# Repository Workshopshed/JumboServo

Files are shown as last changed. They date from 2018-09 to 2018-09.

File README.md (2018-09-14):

# JumboServo
## A jumbo sized servo controlled with I2C

This project was created provide the motion for the Robotic Water Sentry (aka Triffid) and control the motion of the nozzle. 

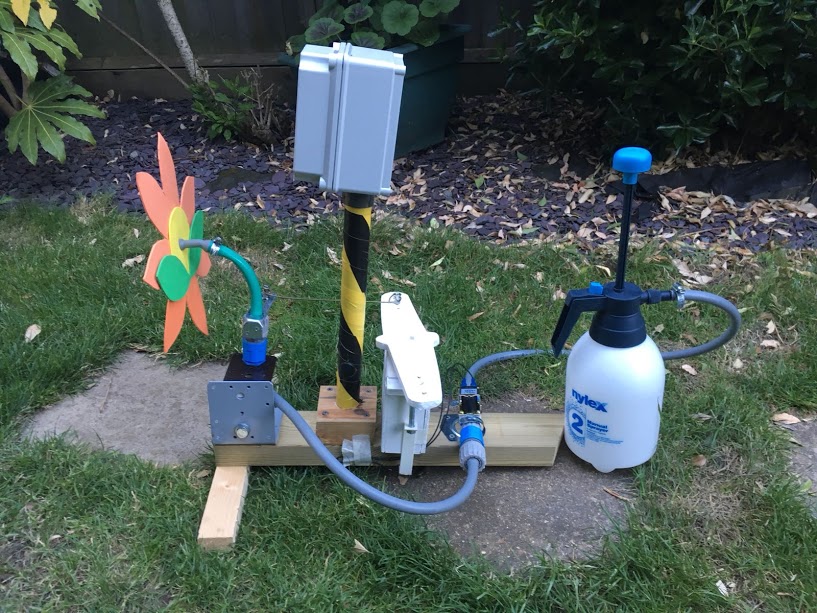
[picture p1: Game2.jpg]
Squirting water game


As big servos were expensive I thought I could build one from an Arduino, Potentiometer and and small Motor with Gearbox.

## Parts

* Adafruit 5v Itsybitsy
* L298 H-Bridge module
* 10K Linear Potentiometer
* 2x 220R resistor
* 0.1uF Capacitor
* Wire
* Connectors
* Motor with gearbox

Along with the electronics is a metal plate to hold the motor and potentiometer and a wooden case styled in the design of a servo. I used a [MFA/COMODRILLS 919D motor gearbox](https://www.mfacomodrills.com/gearboxes/919d_series.html).

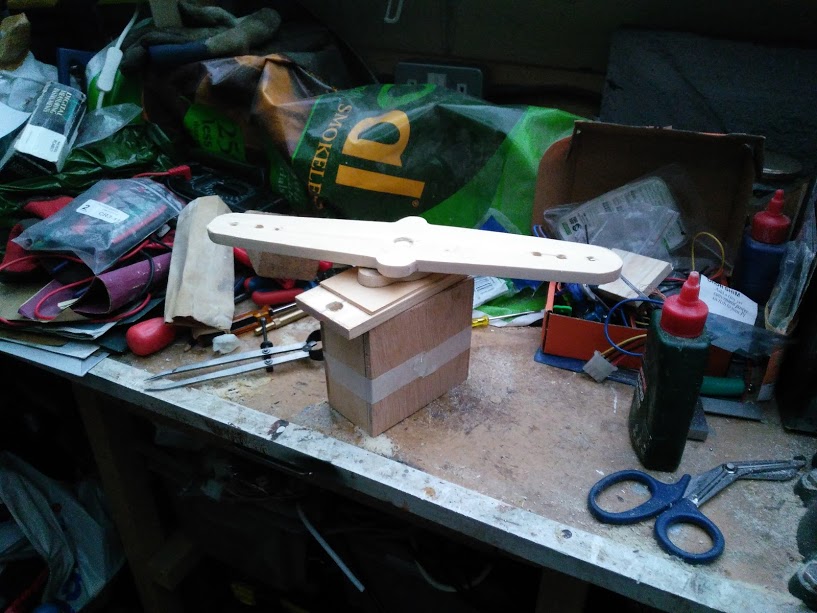
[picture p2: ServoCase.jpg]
Servo Case


## Electronics

The schematic for the project is provided in KiCad format.

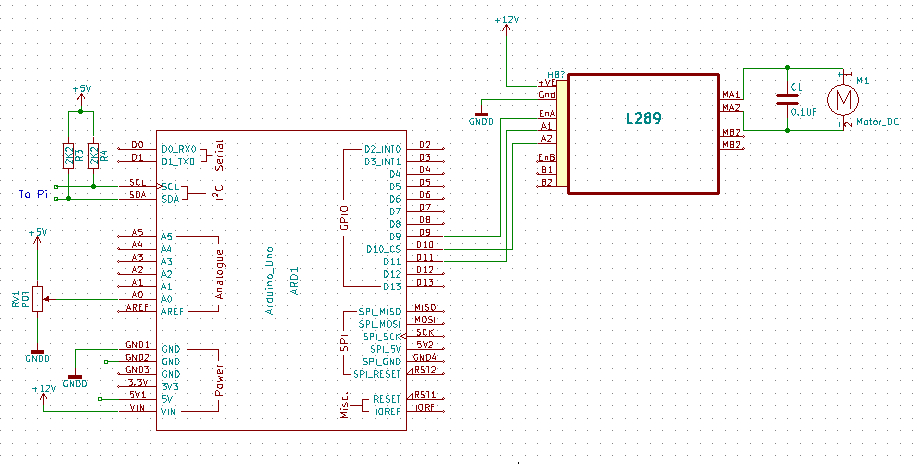
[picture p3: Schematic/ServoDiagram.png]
Schematic Servo Diagram


The key points are that the enable wire for the H-Bridge module should be one of the PWM enabled pins on your Arduino. The two control pins should be determined so that when the motor is running forward the values from the analogue input increments and vice-versa. It's recommended that you test this with the gear for the potentiometer disconnected.

A 0.1uF capacitor is wired across the contacts of the motor to help surpress noise from the motor.

The i2C cable will need some pullup resistors. The value of these will depend on the length of the cable. The longer the cable the lower values are recommended. At 0.5 I used a 220R resistor. Cables over 1m may not work at all.

## Code

There's two lots of code here. The "Servo" folder is the code that runs on the servo and the "Controller" folder is demo project for a test rig with uses an LCD and some buttons to control the servo.

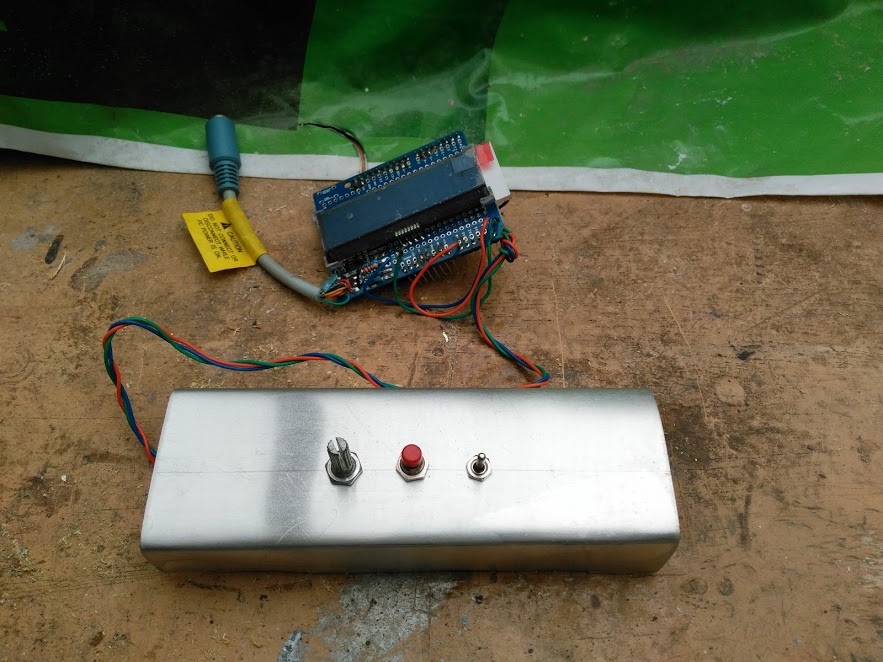
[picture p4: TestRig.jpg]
Test Rig


## Protocol

The servo takes 3 commands from the controller.

|Command|Value|Data Bytes|
|---|---|---|
|Stop |1|0|
|Angle|2|2|
|Speed|3|2|

For the angle and speed commands the command value is followed by the value as an integer with the low byte first. Angle is a value from 0-1023, the controller needs to compensate for this and turn the value into degrees. Note that for the current version speed is just from 0-255 so a 0 should be sent as the high byte. Low values of speed should be avoided typically the motor won't turn.

One of the reasons for having a digital protocol is to be able to read the status back from the servo. This is done by requesting a read from the registers.

|Register|Value|Description|
|---|---|---|
|Target|0|Where the motor is aiming to get to?|
|Running|1|Is the motor currently running?|
|Position|2|Current output shaft position|
|Speed|3|Speed|
|Direction|4|Current direction of movement|

## 3D Models

There are two models provide the gear to fit the potentiometer and the spindle for the output shaft. These were built using OpenSCAD. Note that you may need to adjust the internal size of the gear and spindle to get a good fit on your pot/motor output shaft.

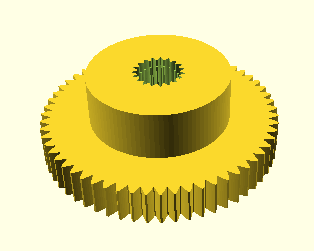
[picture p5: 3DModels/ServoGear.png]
Servo Gear
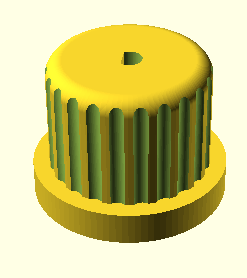
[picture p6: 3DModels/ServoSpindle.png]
Servo Spindle


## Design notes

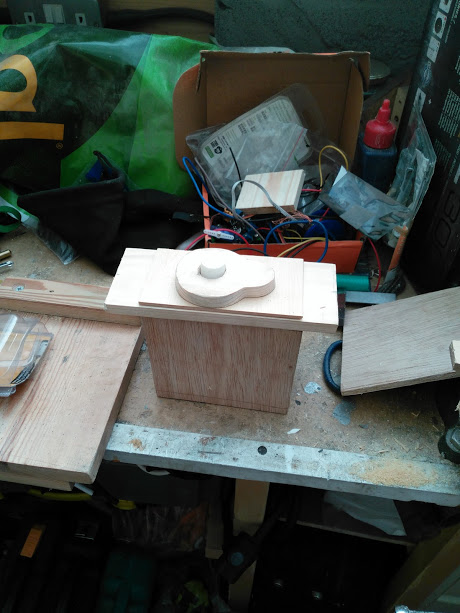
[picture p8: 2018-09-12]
ServoCase2.jpg

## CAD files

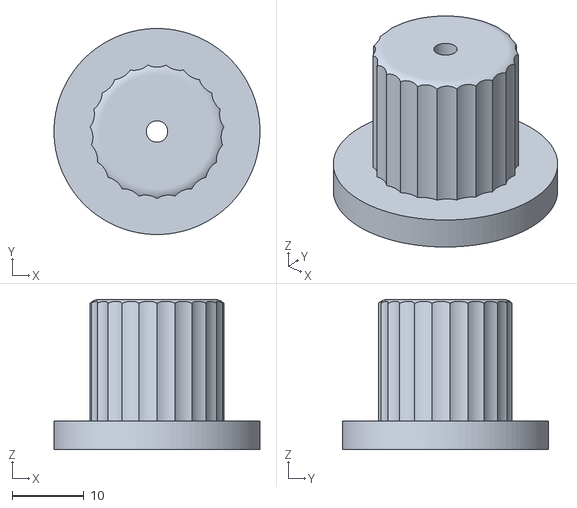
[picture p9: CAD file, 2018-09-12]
3DModels/ServoSpindle.stl
28.8 x 28.8 x 21.0

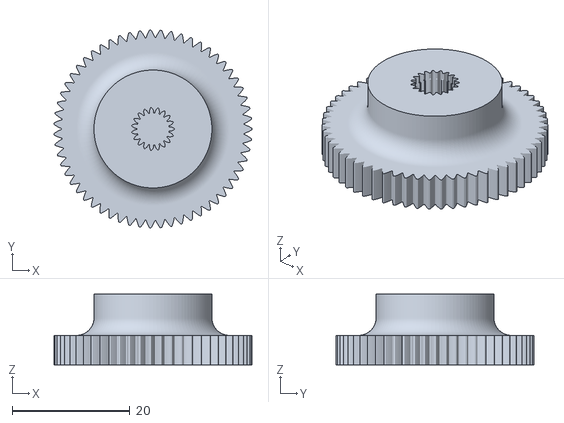
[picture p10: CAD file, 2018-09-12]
3DModels/ServoGear.stl
33.6 x 33.6 x 12.0

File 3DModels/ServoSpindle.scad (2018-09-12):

//Servo Spindle

module ForCircle(offset,num) {
    angle = 360 / num;
    for (i = [1:num] )
        {
            rotate([0,0,angle*i])
                translate([0,offset,0])
                    children();
        }
}

module Torus(r1,r2) {
    rotate_extrude(angle = 360, convexity = 2)
        translate([r2,0,0])
            circle(r=r1);
}

module DrillWithFlat(rdrill,height) {
    flat = rdrill*2;
    difference(){
        cylinder(h=height,r=rdrill);
        translate([rdrill*0.8,-flat/2,-1])
            cube([flat,flat,height+2]);
    }
}

module Spindle()
{
rmajor = 12;
hknurlled = 15;
rtorus = 2;
rindent = 3;
rdrill = 3.15;
hflange =4;
difference() {
    union() {
        difference() {
            union() {
                translate([0,0,hknurlled])
                    Torus(rtorus,rmajor-(2*rtorus));
                cylinder(h=hknurlled,r=rmajor);
                cylinder(h=hknurlled+rtorus,r=rmajor-(2*rtorus));
            }
            ForCircle(hknurlled-rindent,23) {
                translate([0,0,-1])
                    cylinder(h=hknurlled + rtorus + 2,r=rindent);
                }
            }
        translate([0,0,-hflange])
            cylinder(h=hflange,r=rmajor*1.2);
        }
    translate([0,0,-hflange-7]) {
        DrillWithFlat(rdrill,hknurlled + rtorus+1 );
    }
    translate([0,0,hknurlled-hflange-9]) {
        cylinder(h=40,r=1.5);
        } 
    }  
            
}

module drillTest() {
    difference() {
        cylinder(h=3,r=8);
        translate([0,0,-15])
            #DrillWithFlat(3.2, 20);
    }
}

$fn = 100;
Spindle();

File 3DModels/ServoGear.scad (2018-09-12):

// Copyright 2011 Cliff L. Biffle.
// This file is licensed Creative Commons Attribution-ShareAlike 3.0.
// http://creativecommons.org/licenses/by-sa/3.0/

// You can get this file from http://www.thingiverse.com/thing:3575
use <parametric_involute_gear_v5.0.scad>

// Couple handy arithmetic shortcuts
function sqr(n) = pow(n, 2);
function cube(n) = pow(n, 3);

// This was derived as follows:
// In Greg Frost's original script, the outer radius of a spur
// gear can be computed as...
function gear_outer_radius(number_of_teeth, circular_pitch) =
	(sqr(number_of_teeth) * sqr(circular_pitch) + 64800)
		/ (360 * number_of_teeth * circular_pitch);

// We can fit gears to the spacing by working it backwards.
//  spacing = gear_outer_radius(teeth1, cp)
//          + gear_outer_radius(teeth2, cp);
//
// I plugged this into an algebra system, assuming that spacing,
// teeth1, and teeth2 are given.  By solving for circular pitch,
// we get this terrifying equation:
function fit_spur_gears(n1, n2, spacing) =
	(180 * spacing * n1 * n2  +  180
		* sqrt(-(2*n1*cube(n2)-(sqr(spacing)-4)*sqr(n1)*sqr(n2)+2*cube(n1)*n2)))
	/ (n1*sqr(n2) + sqr(n1)*n2);


module servo_gear() {
    $fn = 100;
	n1 = 38; n2 = 59;
	p = fit_spur_gears(n1, n2, 26.8);
    //p=129.3875;
	// Simple Test:
	/* gear (circular_pitch=p,
		gear_thickness = 3,
		rim_thickness = 3,
		hub_thickness = 3,
	    number_of_teeth = n1,
		circles=8);
	
	translate([gear_outer_radius(n1, p) +   gear_outer_radius(n2, p),0,0])
    */
    
    difference() {
        
    union() {
    //fillet
    difference() {
        cylinder(d=26,h=8);
        translate([0,0,8])
            torus(3,13);
    }    
	gear (circular_pitch=p,
		gear_thickness = 5,
		rim_thickness = 5,
		hub_thickness = 12,
    	hub_diameter=20,
        bore_diameter=0,
		circles=0,
		number_of_teeth = n2,
		rim_width = 1);
    }
        
        
    translate([0,0,4])
        splinegear();
    translate([0,0,11])
        cylinder(d=6,h=10);
        
    }
}

module testgear()
{
        n1 = 38; n2 = 59;
        p = fit_spur_gears(n1, n2, 26.8);
        //  96.4527;
        //p=96.4527;
        //14.7358
        $fn = 100;
        
        echo ("Module:",p);
    difference() {
    	gear (circular_pitch=p,
		gear_thickness = 2,
		rim_thickness = 2,
		hub_thickness = 2,
    	hub_diameter=20,
        bore_diameter=0,
		circles=0,
		number_of_teeth = n2,
		rim_width = 1);
        translate([-7,-5,1.5]) linear_extrude(height=3,convexity = 10, twist = 0) text(text=str(n2));
    }
}

module splinegear() {
    n1 = 38; n2 = 59;
	p = fit_spur_gears(n1, n2, 27);
    gear (circular_pitch=p/1.6,
            gear_thickness = 10,
            rim_thickness = 10,
            hub_thickness = 5,
            bore_diameter=0,
            circles=0,
            number_of_teeth = 19,
            rim_width = 10);
}

module splinetest() {
    $fn = 100;
	n1 = 38; n2 = 59;
	p = fit_spur_gears(n1, n2, 27);
    difference() {
        cylinder(d=10,h=6);
        translate([0,0,2])
            splinegear();
    }
}

module torus(r1,r2) {
    rotate_extrude(angle = 360, convexity = 2)
        translate([r2,0,0])
            circle(r=r1);
}

//splinetest();
servo_gear();
//projection(cut = true)
//    translate([0,0,-2])
//testgear();

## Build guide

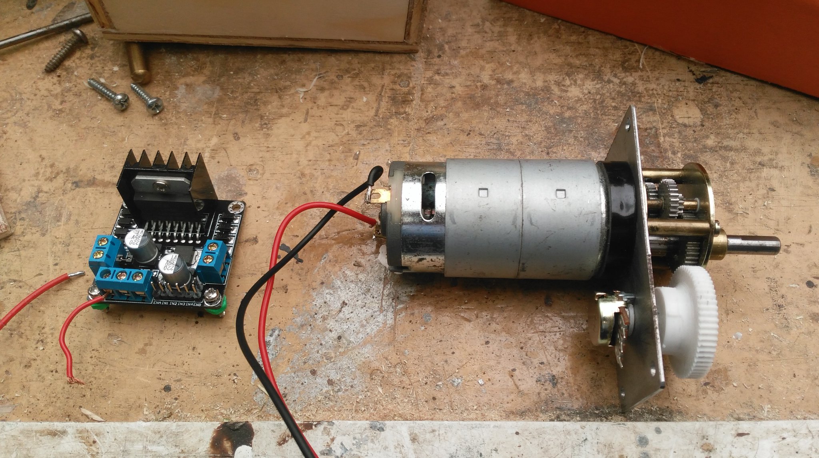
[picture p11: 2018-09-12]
WiringTheMotor.jpg

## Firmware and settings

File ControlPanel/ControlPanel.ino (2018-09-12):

#include <Wire.h>
#include "ST7036.h"
#include "bin.h"
#include "PinChangeInt.h"

//Hardware required:
//1: I2C LCD connected on standard pins
//2: Linear Pot connected on analog pin 1
//3: Jumbo Servo on I2C
//4: Push button connected to GND and pin 9

long sensorValue = 0;  // variable to store the value coming from the sensor
long angle = 0;
ST7036 lcd = ST7036 ( 2, 16, 0x7C );                               //Gotcha with the address, needed to be shifted one to the left

const int slaveAddress = 8;
const int triggerPin = 9;
const int switchPin = 11;
const int potPin = A0;
const int speedValue = 130; // 0 to 255

volatile byte triggered = 0;

enum registers {ReadReg = 0,
                Status = 0,
                Position = 1,
                Angle = 2,
                Speed = 3}; 

const int numReadings = 10;

int readings[numReadings];      // the readings from the analog input
int readIndex = 0;              // the index of the current reading
int total = 0;                  // the running total
int average = 0;                // the average

//Large chars
char bn1[]={6,1,6, 1,6,32, 1,3,4, 3,3,4, 6,2,2,   6,3,1, 5,3,1, 1,1,4,   5,3,4, 5,3,4};
char bn2[]={6,2,6, 2,6,2,  5,2,2, 2,2,4, 32,6,32, 2,2,4, 5,2,4, 32,6,32, 5,3,4, 32,32,6};

void setup()
{
    pinMode(triggerPin, INPUT_PULLUP);  // Configure the pin as an input, and turn on the pullup resistor.
                                      // See http://arduino.cc/en/Tutorial/DigitalPins
    attachPinChangeInterrupt(triggerPin, interruptFunction, FALLING);

    lcd.init();
    lcd.on();
    lcd.setCursor(0, 0);
   
    lcd.print("Hello BCS!");
    
    loadlargechars();
    
    delay(2000);
    lcd.clear();
}

// Do not use any Serial.print() in interrupt subroutines. Serial.print() uses interrupts,
// and by default interrupts are off in interrupt subroutines. Interrupt routines should also
// be as fast as possible. Here we just increment a counter.
void interruptFunction() {
  triggered = 1;
}

void loadlargechars()
{
  uint8_t cc1[8] = { // Custom Character 1
     B8(11111),
     B8(11111),
     B8(11111),
     B8(00000),
     B8(00000),
     B8(00000),
     B8(00000),
     B8(00000)
     };

  uint8_t cc2[8] = { // Custom Character 2
     B8(00000),
     B8(00000),
     B8(00000),
     B8(00000),
     B8(00000),
     B8(11111),
     B8(11111),
     B8(11111)
     };

  uint8_t cc3[8] = { // Custom Character 3
     B8(11111),
     B8(11111),
     B8(11111),
     B8(00000),
     B8(00000),
     B8(00000),
     B8(11111),
     B8(11111)
     };

  uint8_t cc4[8] = { // Custom Character 4
     B8(11100),
     B8(11110),
     B8(11111),
     B8(11111),
     B8(11111),
     B8(11111),
     B8(11110),
     B8(11100)
     };
     
  uint8_t cc5[8] = { // Custom Character 5
     B8(00111),
     B8(01111),
     B8(11111),
     B8(11111),
     B8(11111),
     B8(11111),
     B8(01111),
     B8(00111)
     };     

  uint8_t cc6[8] = { // Custom Character 6
     B8(11111),
     B8(11111),
     B8(11111),
     B8(11111),
     B8(11111),
     B8(11111),
     B8(11111),
     B8(11111)
     };   

  uint8_t cc7[8] = { // Custom Character 7 Degree
     B8(01110),
     B8(10001),
     B8(10001),
     B8(10001),
     B8(01110),
     B8(00000),
     B8(00000),
     B8(00000)
     };  
    
    lcd.load_custom_character(1, cc1);
    lcd.load_custom_character(2, cc2);
    lcd.load_custom_character(3, cc3);
    lcd.load_custom_character(4, cc4);
    lcd.load_custom_character(5, cc5);
    lcd.load_custom_character(6, cc6);
    lcd.load_custom_character(7, cc7);
}

int getReading()
{
  total = total - readings[readIndex];
  // read from the sensor:
  readings[readIndex] = analogRead(potPin);
  // add the reading to the total:
  total = total + readings[readIndex];
  // advance to the next position in the array:
  readIndex = readIndex + 1;

  // if we're at the end of the array...
  if (readIndex >= numReadings) {
    // ...wrap around to the beginning:
    readIndex = 0;
  }

  // calculate the average:
  average = total / numReadings;
  return average;
}

void loop()
{
  if (triggered == 1) {
    lcd.clear();
    lcd.print("Sending");
    writeRegister(Speed,speedValue);
    writeRegister(Angle,sensorValue); //Values 0-1023
    delay(700);
    lcd.clear();
    lcd.print("Sent");
    delay(500);
    lcd.clear();
    display(angle);
    triggered = 0;    
  }

  
  // read the value from the sensor:
  long newValue = getReading();
  if (sensorValue != newValue) {
    // Makes the assumption that the pot turns 360 degrees, adjust the value below to compensate e.g. a 300 degree pot would be 3000
    angle = (sensorValue * 3600 / 1024); 
    display(angle);
  }
  sensorValue = newValue;

  delay(10);
}

void display(int i) //Display the value in large characters
{
  lcd.clear();  
  //lcd.print(angle);
  PrintBigDeg(15);
  if (i == 0)
  {
    PrintBigDigit(0,8);
    PrintBigDot(11);
    PrintBigDigit(0,12);
  }
  int pos = 15;
  while(i>0)
  {
    pos -= 3;
    PrintBigDigit(i % 10,pos);
    i /= 10;
    if (pos==12){
     PrintBigDot(--pos);
    }
  }
  

}

void PrintBigDigit(uint8_t digit, uint8_t offset)
{

 // Line 1 of the one digit number
 lcd.setCursor(0,offset);
 lcd.write(bn1[digit*3]);
 lcd.write(bn1[digit*3+1]);
 lcd.write(bn1[digit*3+2]);

 // Line 2 of the one-digit number
 lcd.setCursor(1,offset);
 lcd.write(bn2[digit*3]);
 lcd.write(bn2[digit*3+1]);
 lcd.write(bn2[digit*3+2]);
}

void PrintBigDot(uint8_t offset)
{
  lcd.setCursor(1,offset);
  lcd.print('.');
}
void PrintBigDeg(int8_t offset)
{
  lcd.setCursor(0,offset);
  lcd.write(7);
}

void readRegister(byte reg) {
  Serial.print("Reading register:");
  Serial.print(reg);
  
  Wire.beginTransmission(slaveAddress);
  Wire.write((uint8_t *)&reg, sizeof(reg));
  Wire.endTransmission();
  delay(100);
  Wire.requestFrom(slaveAddress, 2);    // request 2 bytes from slave device #8

  int value;
  if (Wire.available()) { // slave may send less than requested
    value = Wire.read(); // receive a byte as character
  }
  if (Wire.available()) {
    int high = Wire.read();
    value = value + (high << 8);
  }

  Serial.print("=");    
  Serial.println(value);    

  while (Wire.available()) { // clear buffer incase anything else sent
    char c = Wire.read(); // receive a byte as character
  }
  
  delay(500);
}

void writeRegister(byte command,int value) {
  Serial.print("Writing register:");
  Serial.print(command);
  Serial.print("=");    
  Serial.println(value);    
  char message[3];
  message[0] = command;
  message[1] = value;       //low Byte, high
  message[2] = value >> 8;
  Wire.beginTransmission(slaveAddress);
  Wire.write(message,3);
  Wire.endTransmission();
}

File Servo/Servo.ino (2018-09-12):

#include <Wire.h>

const int slaveAddress = 8;

const int sensePin = A0;
const int drivePin1 = 11;
const int drivePin2 = 10;
const int speedPin = 9; //Needs to support PWM

int blink = 0;

short registers[5];
int readCmd;

enum readRegisters { Target = 0,
                     Running = 1,
                     Position = 2,
                     Speed = 3,
                     Direction = 4
                   };

enum commands { CmdStop = 1,
                CmdAngle = 2,
                CmdSpeed = 3,
              };

void setup() {
  Serial.println("Initialising");
 
  stop();

  pinMode(drivePin1, OUTPUT);
  pinMode(drivePin2, OUTPUT);
  pinMode(speedPin, OUTPUT);
  pinMode(sensePin, INPUT);

  Wire.begin(slaveAddress);                // join i2c bus with address #8
  Wire.onReceive(receiveEvent); // write data
  Wire.onRequest(requestEvent); // requests to read data

}

void clearAndHome() 
{ 
  Serial.write(27); 
  Serial.print("[2J"); // clear screen 
  Serial.write(27); // ESC 
  Serial.print("[H"); // cursor to home 
} 

void loop() {
  digitalWrite(13, blink);
  blink = !blink;
  
  registers[Position] = analogRead(sensePin);

  if (registers[Running]) {
    clearAndHome();
    Serial.println(registers[Target]);
    Serial.println(registers[Position]);
    Serial.println(registers[Speed]);
    
    if (registers[Direction] == 1) {
      Serial.println("Forward");
      if (registers[Position] >= registers[Target]) {
        stop();
      }
    }
    if (registers[Direction] == -1) {
      Serial.println("Backwards");
      if (registers[Position] <= registers[Target]) {
        stop();
      }
    }
  }
}

void stop() {
  digitalWrite(drivePin1, LOW);
  digitalWrite(drivePin2, LOW);
  analogWrite(speedPin, 0);
  registers[Running] = false;
}

// function that executes whenever data is received from master
// this function is registered as an event, see setup()
void receiveEvent(int bytesReceived) {
  char command;
  int value;
  int lowB;
  int highB;

  switch (bytesReceived) {
    case 1:
      //Read request register
      readCmd = Wire.read();
      break;
    case 3:
      command = Wire.read(); // receive byte as a character
      //Pi is low endian
      lowB = Wire.read();
      highB = Wire.read();
      value = (highB << 8) | lowB;

      switch (command) {
        case CmdStop:
          stop();
          break;
        case CmdAngle:
          registers[Target] = value;
          registers[Running] = true;
          if (registers[Target] > registers[Position]) {
            registers[Direction] = 1;
            digitalWrite(drivePin1, LOW);
            digitalWrite(drivePin2, HIGH);
          }
          else {
            registers[Direction] = -1;
            digitalWrite(drivePin2, LOW);
            digitalWrite(drivePin1, HIGH);
          }
          analogWrite(speedPin, registers[Speed]);        
          break;
        case CmdSpeed:
          registers[Speed] = value;
          analogWrite(speedPin, registers[Speed]);
          break;

      }
      break;
    default:
      for (int a = 0; a < bytesReceived; a++) {
        Wire.read();  // throw buffer away so we can read again
      }
  }
}

// function that executes whenever data is requested by master
// this function is registered as an event, see setup()
// Don't add serial print to this routine, it will stop it sending messages back

void requestEvent() {

  short value = registers[readCmd];
  Wire.write((uint8_t *)&value, sizeof(value));

}

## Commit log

2018-09-12 Servo
    Servo code
2018-09-12 3d Models
    Models for the spindle and gear
    [ServoGear.scad, ServoGear.stl, ServoSpindle.scad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]
2018-09-14 Schematic
    Electronics diagram from KiCad
    [Servo.sch]
2018-09-14 3D Models
    Moved the folder, added description to readme.
    Updated readme with more details
    [ServoGear.scad, ServoGear.stl, ServoSpindle.scad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]
2018-09-14 Readme
    Fixed linked for schematic
2018-09-14 Readme
    Notes on I2C pullups
